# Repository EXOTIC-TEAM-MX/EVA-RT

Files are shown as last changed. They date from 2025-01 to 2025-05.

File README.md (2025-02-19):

# EVA-RT
EVA-RT is the new robotracer series with centrifugal fan and side sensors for curve and goal marks. Created in December 2024 to participate in the All Chile robot Contest 2025, obtaining good results despite its simplicity.

Achievements:
- ACRC2025 - 1st and 2nd place

This repository contains the details, source code, 3D models, PCB files of the robot and EasyEDA proyect available for editing and exporting!

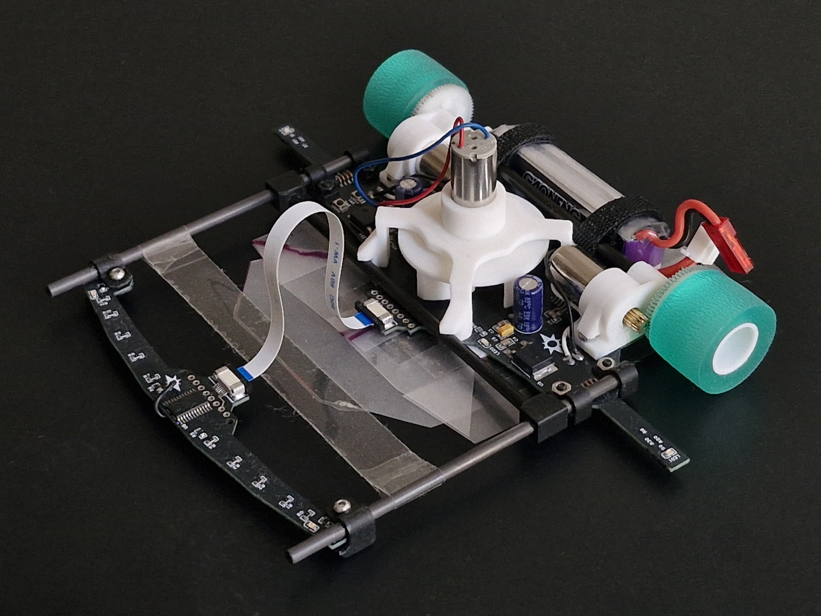
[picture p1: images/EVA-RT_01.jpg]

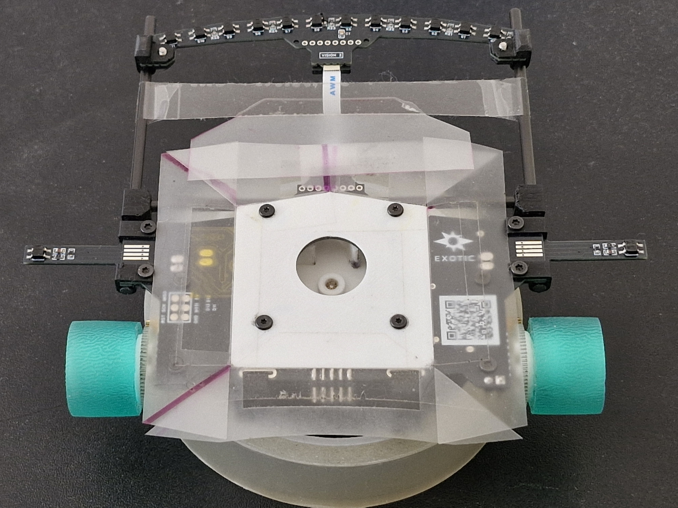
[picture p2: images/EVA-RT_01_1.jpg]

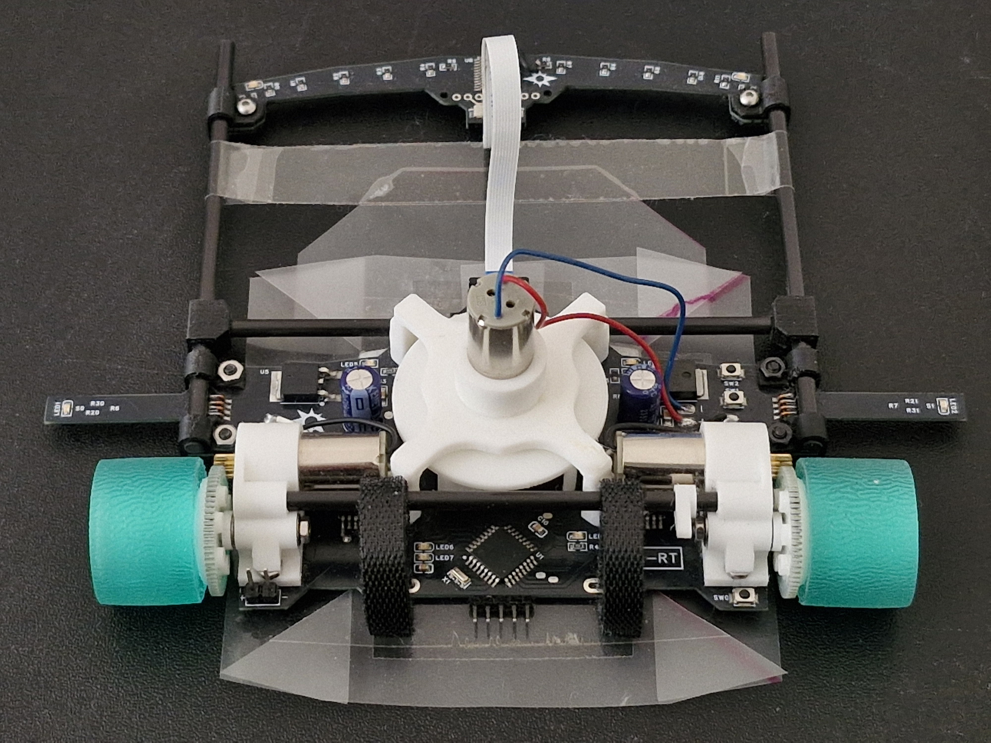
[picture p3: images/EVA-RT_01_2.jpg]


# DETAILS
- Name: EVA-RT
- PCB thickness: 1mm
- Dimensions: 117 x 146 x 38 mm
- Weight: 89g
- MCU: ATMEGA328P-AU
- Line sensor: 12x QRE1113GR
- Side sensor: 2x QRE1113GR
- Motor: 3x coreless 1020 7.4V (unknown model)
- Motor Driver: 2x IFX9201SG, RM10N100LD
- Battery: GAONENG 2S 7.4V 300mAh (80C/160C)
- Gears (M0.3): Spur 64T, pinnion 11T
- Wheel tires: printer rollers (unknown model)

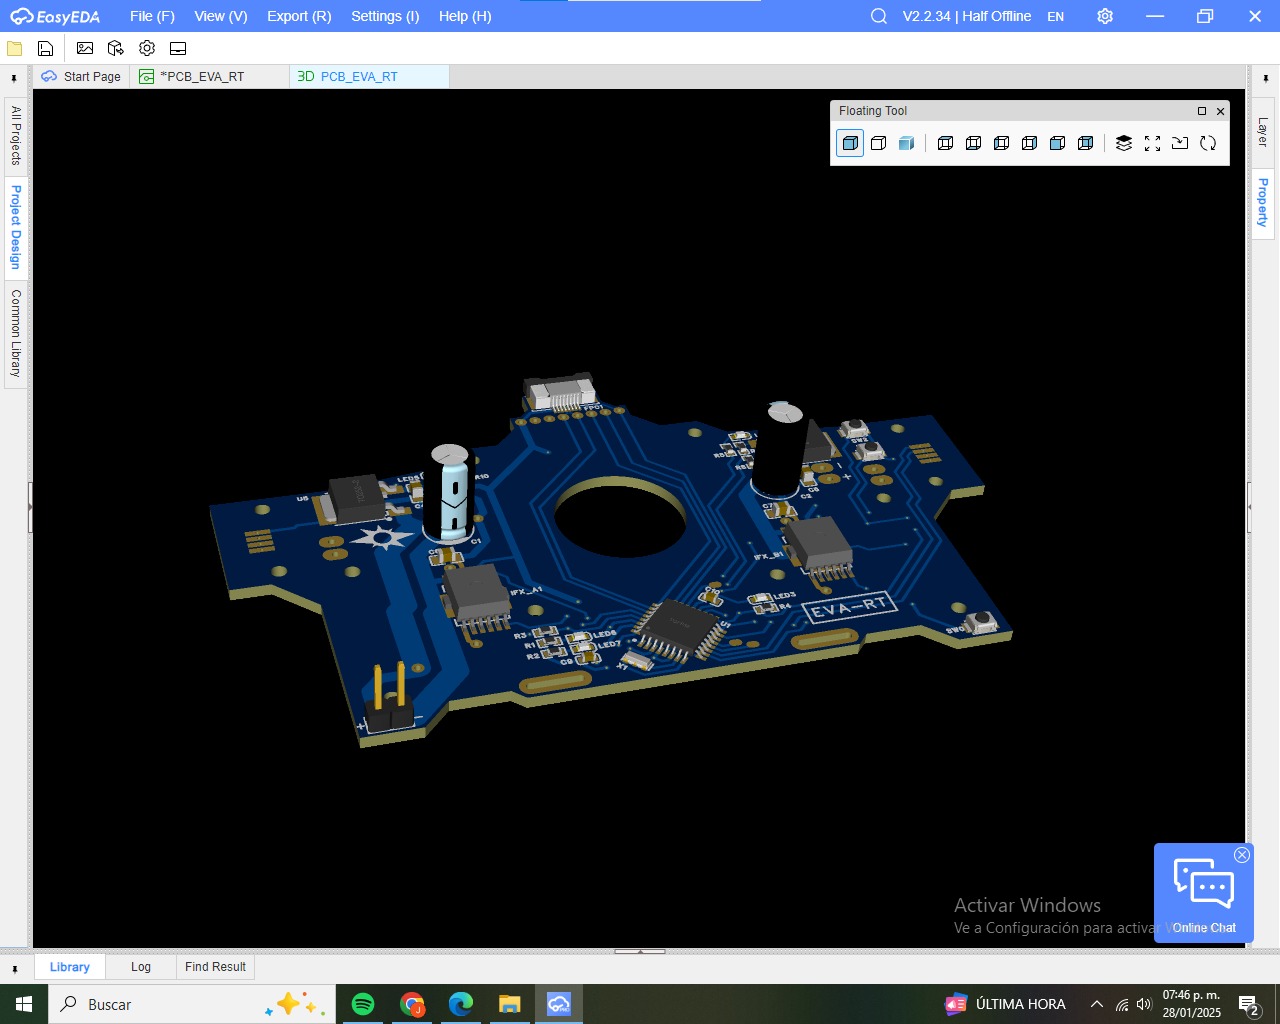
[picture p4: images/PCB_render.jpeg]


# ENVIROMENT
- Arduino IDE 2.0.2
- Autodesk Fusion 360
- EasyEDA-ProV2.2.34.8

#  Robotracer EVA-RT01 code LITE1.0 test
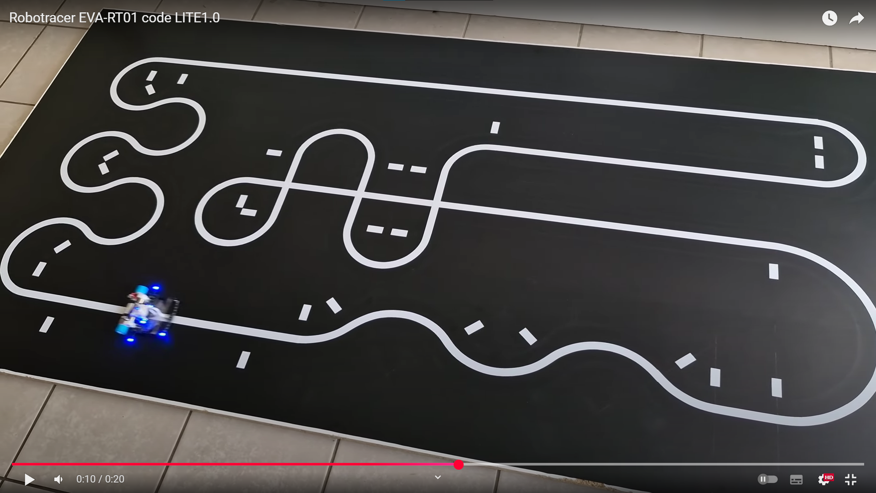
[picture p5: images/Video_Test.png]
(https://youtu.be/mkbgixV5h3M)


# LICENSE
This repository is released under the GNU Affero General Public License v3.0.

©  EXOTIC TEAM MX

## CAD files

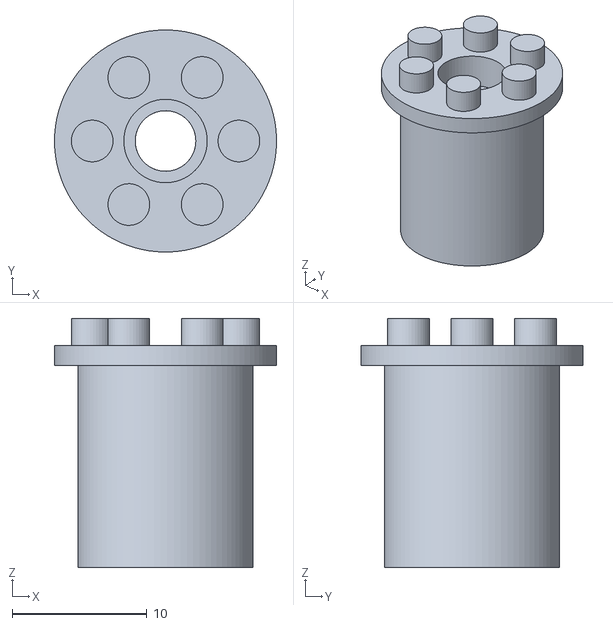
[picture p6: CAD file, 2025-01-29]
3d_models/wheel_rim.stl
16.5 x 16.5 x 18.5

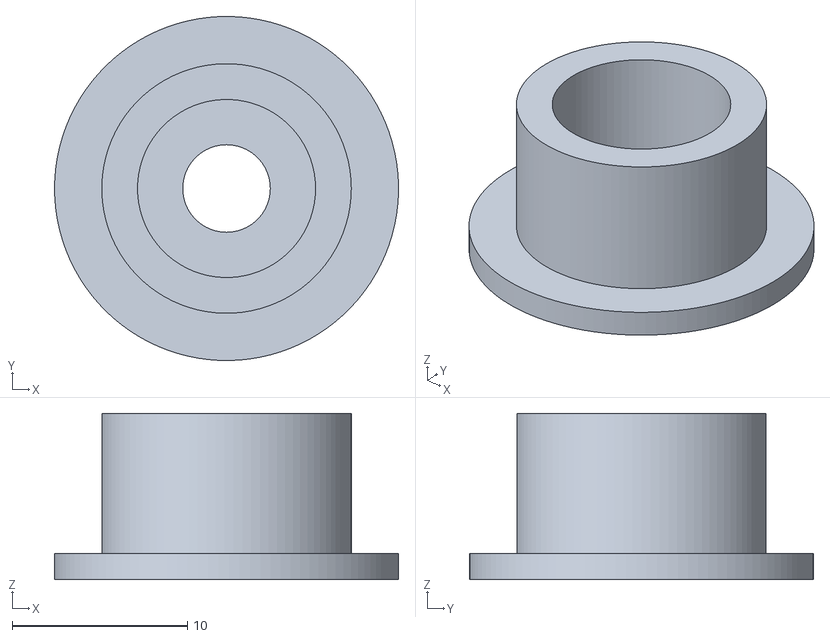
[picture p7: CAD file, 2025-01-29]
3d_models/impeller_base_2.stl
19.6 x 19.6 x 9.50

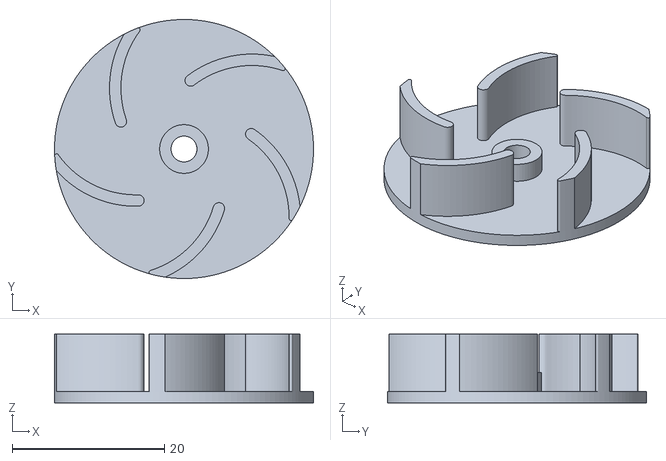
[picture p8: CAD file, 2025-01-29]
3d_models/impeller_fan.stl
34.0 x 34.0 x 9.00

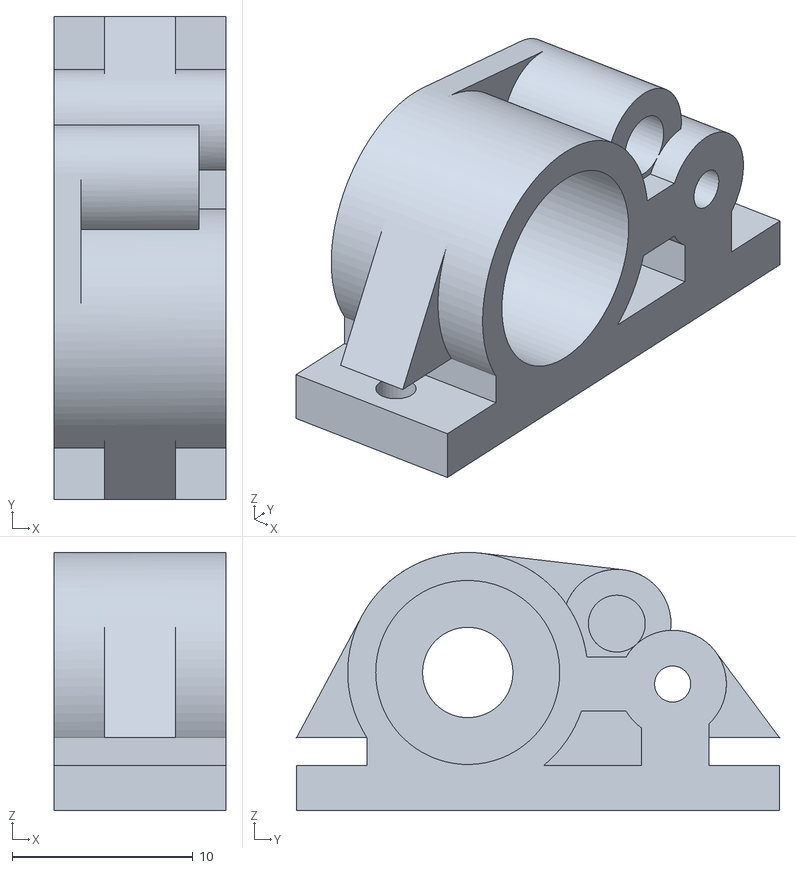
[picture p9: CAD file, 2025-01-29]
3d_models/gearbox.stl
9.50 x 26.7 x 14.3

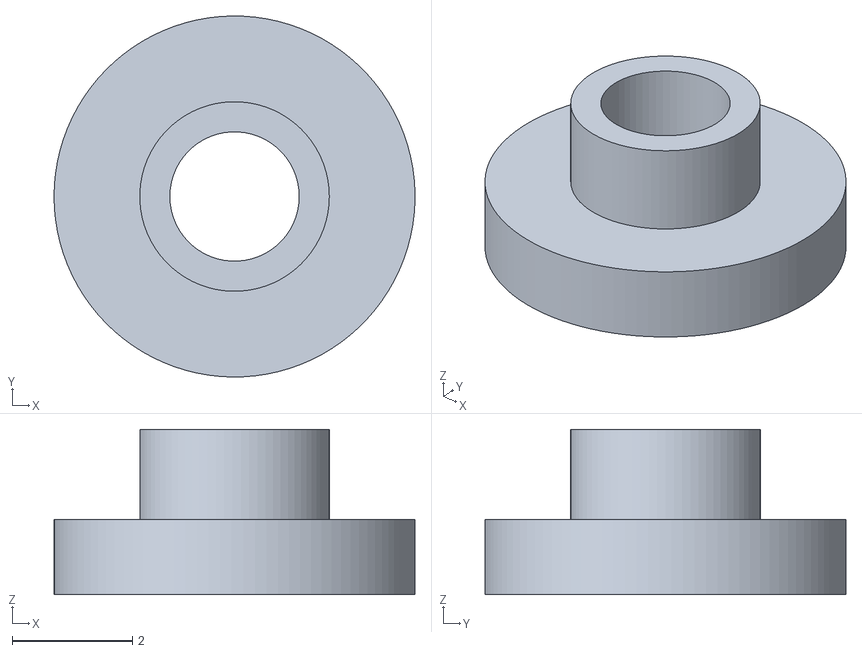
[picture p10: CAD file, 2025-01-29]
3d_models/bead.stl
6.00 x 6.00 x 2.75

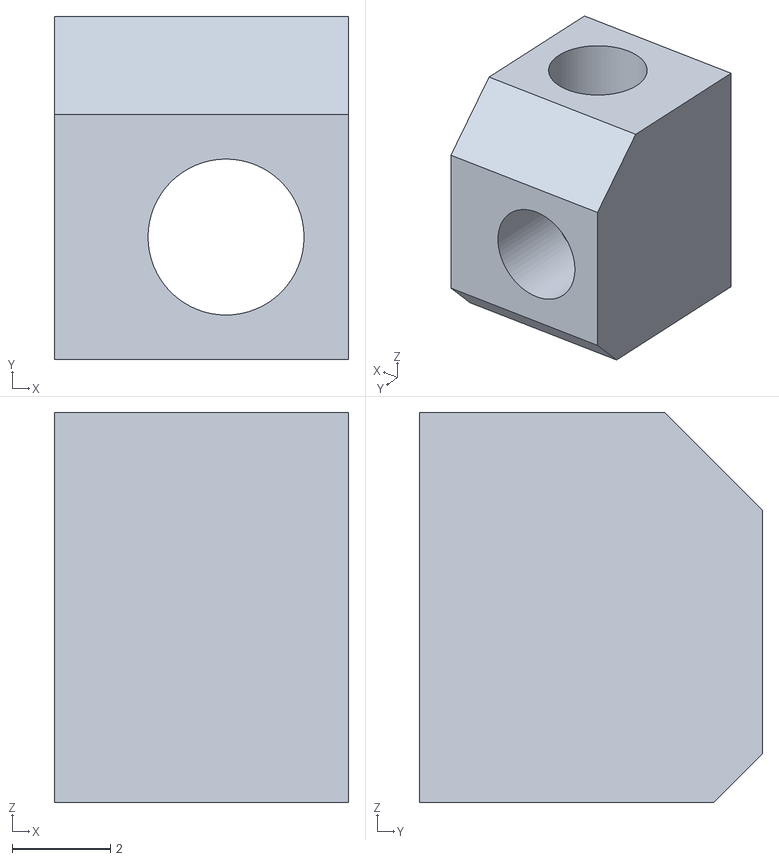
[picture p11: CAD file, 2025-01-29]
3d_models/barilla_connection.stl
6.00 x 7.00 x 7.95

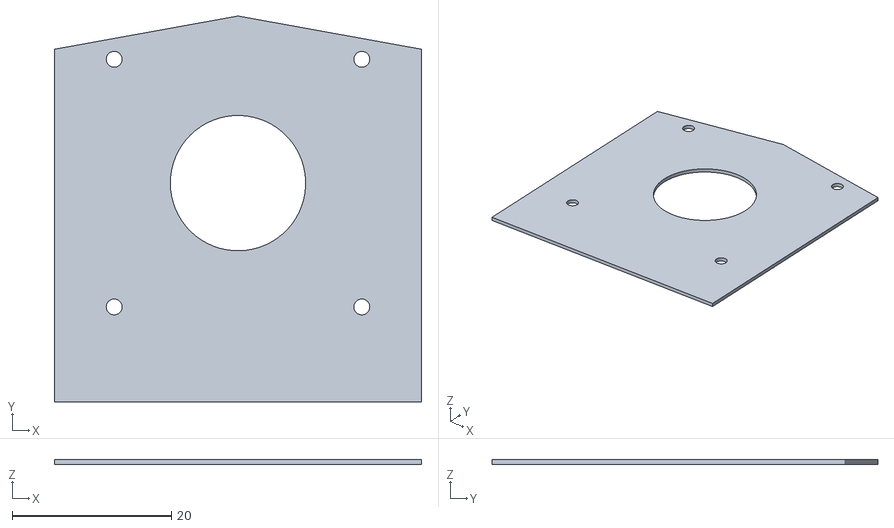
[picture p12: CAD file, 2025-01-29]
3d_models/suction_base.stl
46.2 x 48.5 x 0.6

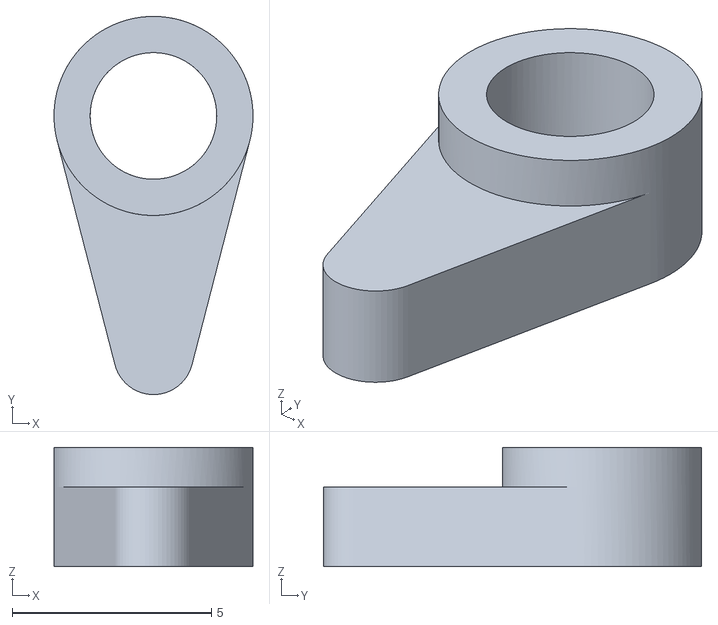
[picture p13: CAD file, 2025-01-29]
3d_models/battery_holder.stl
5.00 x 9.50 x 3.00

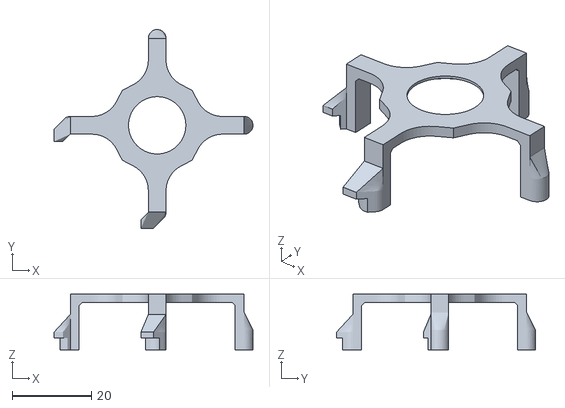
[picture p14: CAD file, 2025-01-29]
3d_models/impeller_base_1.stl
50.4 x 50.4 x 14.1

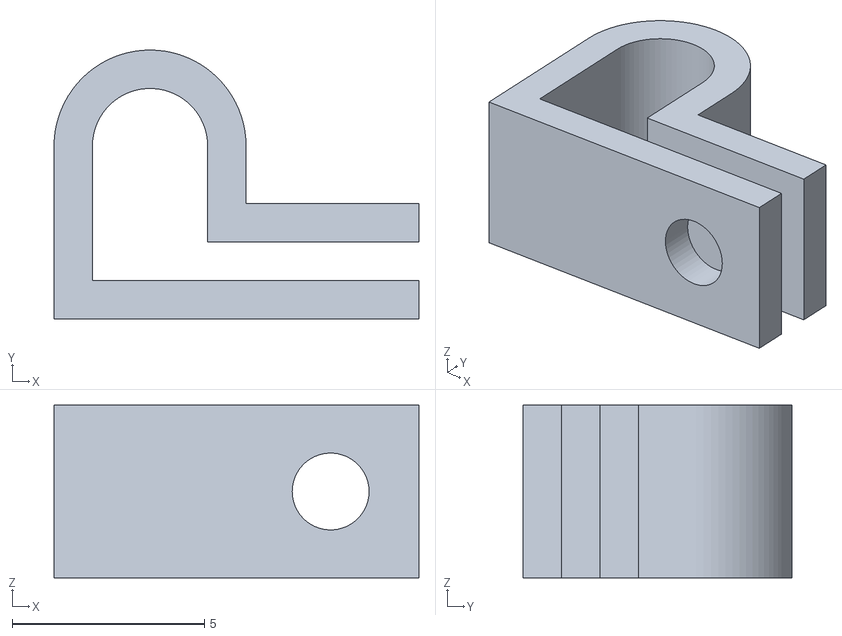
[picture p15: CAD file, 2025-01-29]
3d_models/barilla_clamp.stl
9.50 x 7.00 x 4.50

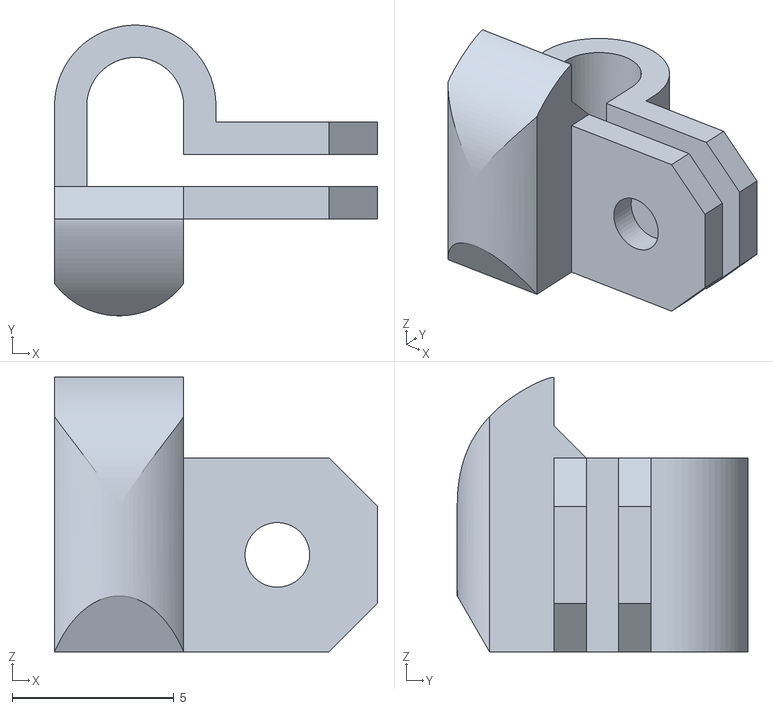
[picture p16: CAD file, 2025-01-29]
3d_models/sensor_sledge.stl
10.0 x 9.00 x 8.50

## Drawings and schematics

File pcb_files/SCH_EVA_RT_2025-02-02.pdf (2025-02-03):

Power Supply & Voltage Regulator | Source Capacitors

## User Interface I/O

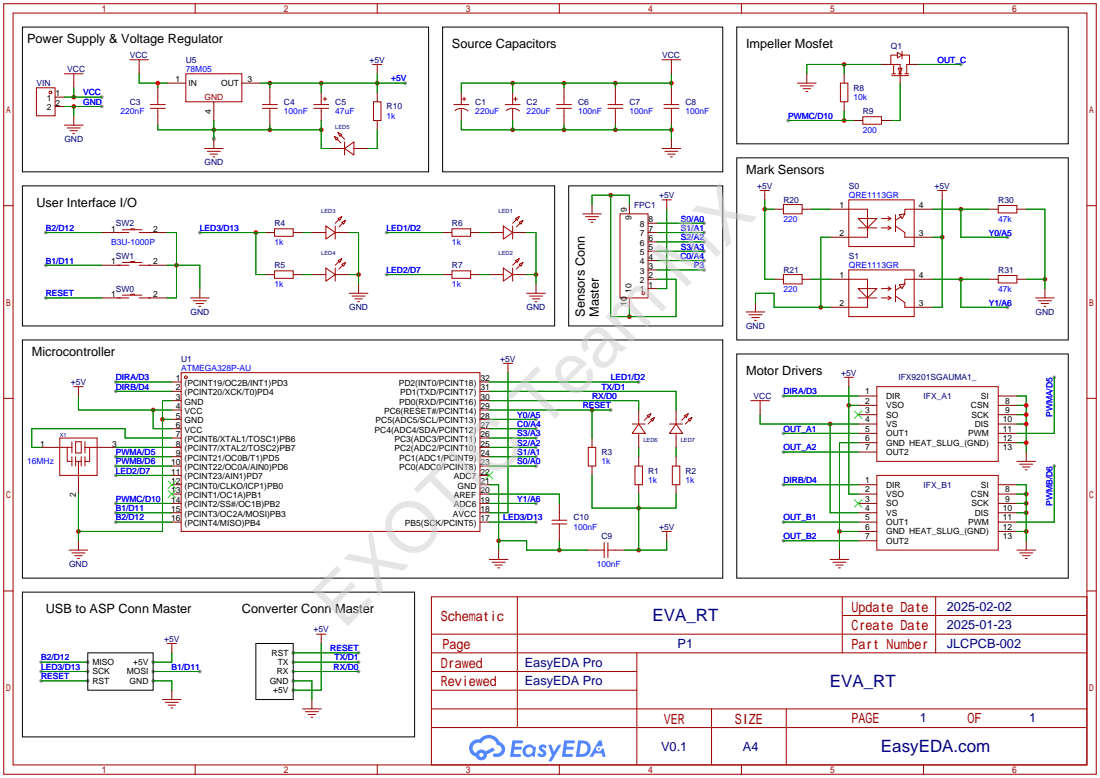
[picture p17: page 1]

USB to ASP Conn Master

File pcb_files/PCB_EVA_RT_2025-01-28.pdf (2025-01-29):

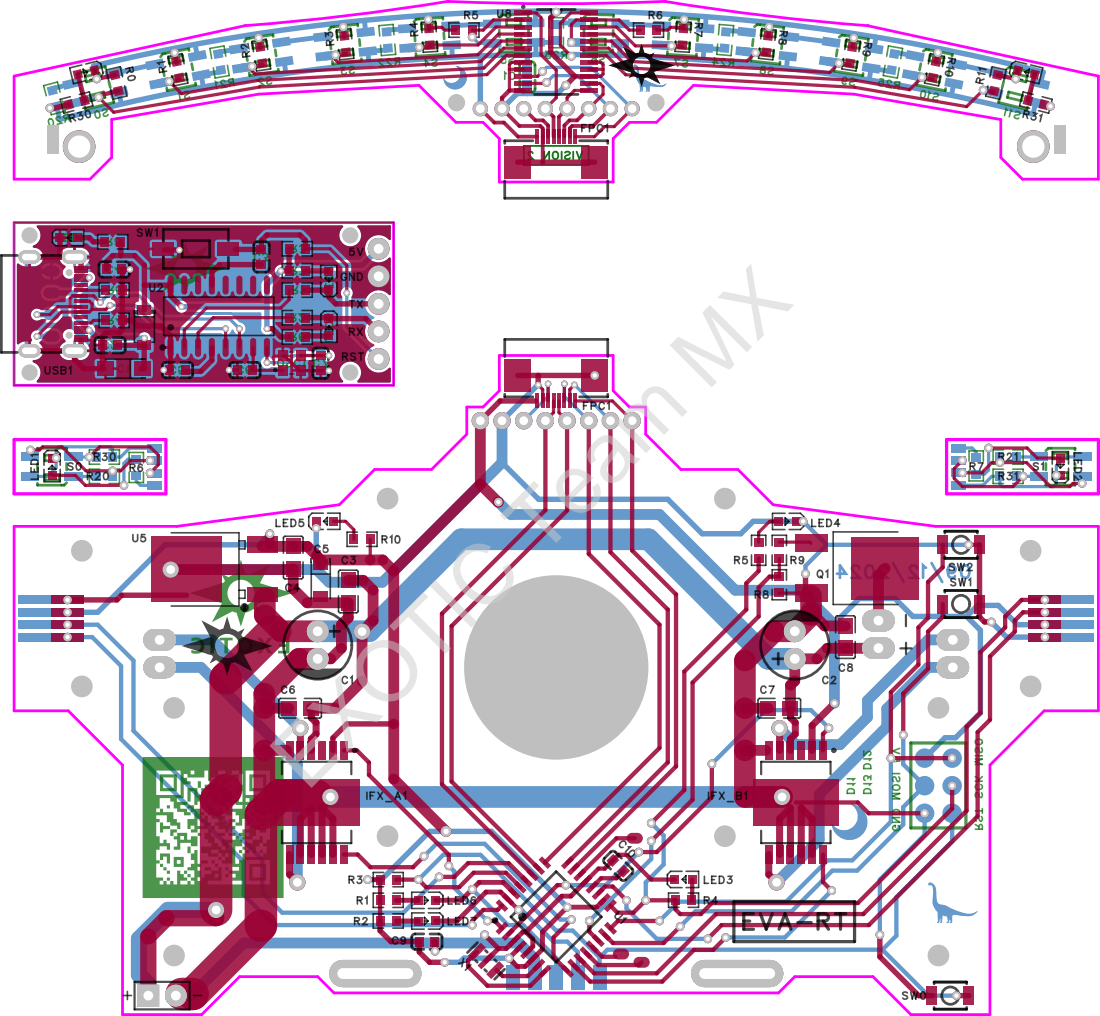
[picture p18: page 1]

U2 | C7LED² LED³ | GND

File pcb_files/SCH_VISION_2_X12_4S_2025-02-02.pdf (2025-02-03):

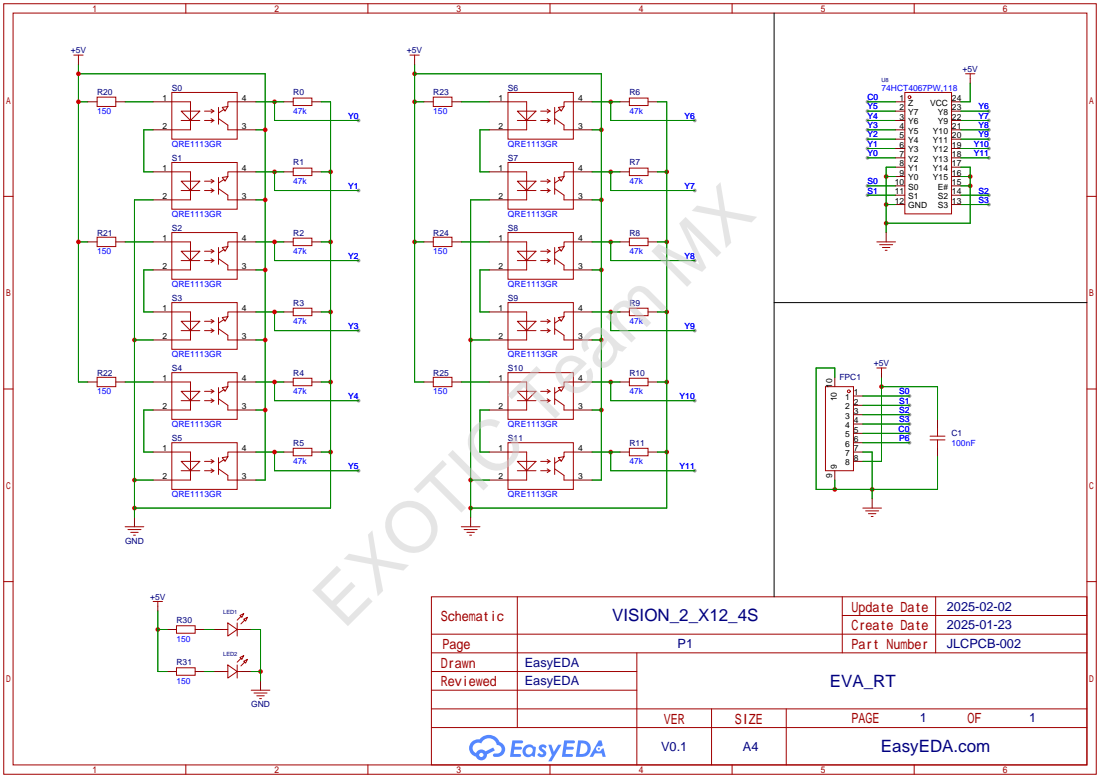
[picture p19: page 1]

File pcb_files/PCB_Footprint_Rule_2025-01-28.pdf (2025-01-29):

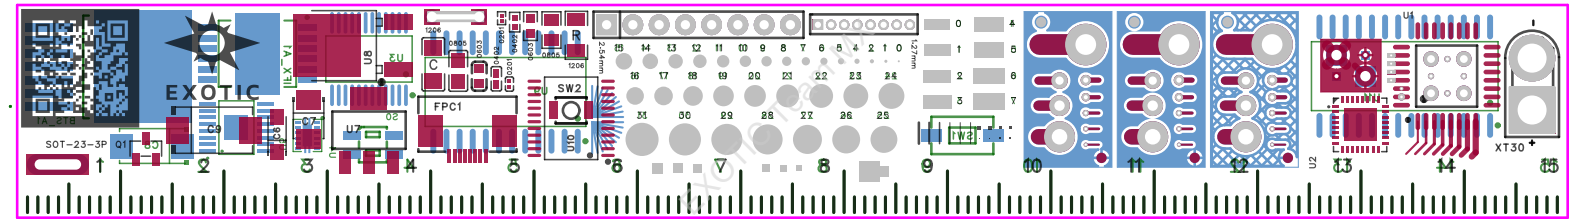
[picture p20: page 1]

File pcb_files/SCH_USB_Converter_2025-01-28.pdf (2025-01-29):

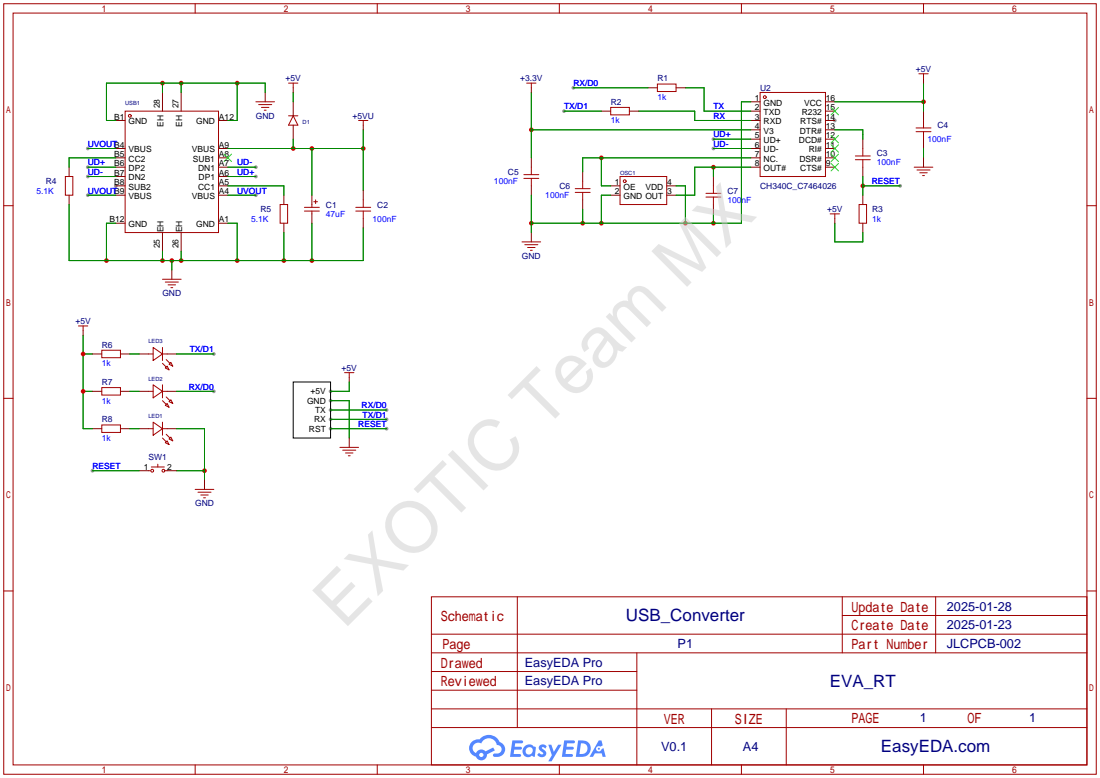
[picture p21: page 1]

DSR# 10 RI# 11 DCD# 12 DTR# 13 RTS# 14 R232 15 VCC 16

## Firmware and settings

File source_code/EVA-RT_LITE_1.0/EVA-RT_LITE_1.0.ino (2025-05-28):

/*
  EVA-RT LITE v1.0 - main code for robotracer EVA-RT series
  
    Created on: Jan, 2025
    Edited by Mauricio Tovar
  
      DRIVERS:            IXF9201SG
      NUMBER OF SENSORS:  12A/3s
      MICROCONTROLLER:    ATMEGA328P-AU
      BATTERY:            2S
      CONTROL:            PD
      MOTORS:             1020

  This code is the simplified version of the program used for
  the All Chile Robot Contest 2025. Conceived and designed to
  facilitate the reading and understanding of the fundamental
  concepts.

  This code consists of the base control of the robot using the
  functions included in the Arduino core library. It includes
  the reading of the side sensors for detecting the goal marker.

  Copyright (C) 2025 EXOTIC TEAM MX

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
  This code is part of the EVA-RT Github repository. See more
  in the next link:
  
  https://github.com/EXOTIC-TEAM-MX/EVA-RT
*/

//  =============================
//  U S E R   P A R A M E T E R S
//  =============================

#define KP 0.04  //  proportional component coefficient (0.04)
#define KD 0.6   //  derivative component coefficient (0.6)

#define SPEED 60       //  base PWM motors speed value (60)(min 20)
#define SPEED_IMP 215  //  base PWM impeller speed value (215)

#define INVERT_SENSOR_READS false  //  white line and black background if false (true = black line)

#define SPEED_TIME_MS 50    //  time until robot gets base speed (50)
#define RUN_TIME_MS 6000    //  time until robot turns off automatically since start running (6000)
#define MAX_OUT_TIME_MS 10  //  maximum time sensors can be out of line until robot turns off (10)

//  =====================================
//  A D V A N C E D   P A R A M E T E R S
//  =====================================

#define OUT_OUTTER_SPEED 255  //  outter side motor PWM value when sensors are offline (255)
#define OUT_INNER_SPEED -255  //  inner side motor PWM value when sensors are offline (-255)
#define MAX_IMP_SPEED 200     //  max impeller PWM value (200)

#define MARK_TIMER_MS 50     //  time while mark state is enabled (50)
#define START_DELAY_MS 1000  //  time before robot start running (1000)
#define STOP_TIME_MS 75      //  time while robot is breaking after is turned off (75)

#define SENSOR_THRESHOLD_PERCENT 75
#define CALIBRATION_NOISE_DIVISOR 8
#define CALIBRATION_AVG_SAMPLES 8
#define CALIBRATION_COLLECTOR_SAMPLES 10

//  ===============================
//  G L O B A L   C O N S T A N T S
//  ===============================

//  user input pins
#define PIN_BUTTON_1 11
#define PIN_BUTTON_2 12
#define PIN_LED_1 2
#define PIN_LED_2 7
#define PIN_LED_3 13

//  sensor pins
#define PIN_SENSORS_MUX_S0 A0
#define PIN_SENSORS_MUX_S1 A1
#define PIN_SENSORS_MUX_S2 A2
#define PIN_SENSORS_MUX_S3 A3
#define PIN_SENSORS_COMMON A4
#define PIN_MARK_SENSOR_0 A5
#define PIN_MARK_SENSOR_1 A6

//  motor driver pins
#define PIN_PWM_A 5
#define PIN_PWM_B 6
#define PIN_PWM_C 10
#define PIN_DIR_A 3
#define PIN_DIR_B 4

#define NUM_SENSORS 12      //  ammount of line sensors
#define NUM_MARK_SENSORS 2  //  ammount of side mark sensors
#define TOTAL_SENSORS (NUM_SENSORS + NUM_MARK_SENSORS)
#define INDEX_MS0 NUM_SENSORS
#define INDEX_MS1 (NUM_SENSORS + 1)
#define FIRST_SENSOR_MUX_SWITCH_CONFIG 2  //  mux switch configuration for first line sensor (S0)
#define LAST_SENSOR_MUX_SWITCH_CONFIG 13  //  mux switch configuration for last line sensor (S11)

//  ===============================
//  G L O B A L   V A R I A B L E S
//  ===============================

int sensorValues[TOTAL_SENSORS];
unsigned int maxSensorValues[TOTAL_SENSORS];
unsigned int minSensorValues[TOTAL_SENSORS];
int sensorThreshold[TOTAL_SENSORS];

bool markState[2];
bool pastMarkSensorValues[2];

unsigned long startTime;              //  instant time before start running
unsigned long currentTime;            //  current time
unsigned long outStartTime;           //  last time before sensors gets offline
unsigned long markRisingEdgeTime[2];  //  instant time when marks sensors reads rising edge

bool isOnLine = false;
bool lastDetectedSide;
bool isRunning = false;
bool isOffEnabled = false;

int speedDecrement = 0;
bool isSpeedBase = false;

int error;
int previousError;

void setup() {
  //  ===================
  //  M A I N   S E T U P
  //  ===================

  //  user I/O interface setup
  pinMode(PIN_BUTTON_1, INPUT_PULLUP);
  pinMode(PIN_BUTTON_2, INPUT_PULLUP);
  pinMode(PIN_LED_1, OUTPUT);
  pinMode(PIN_LED_2, OUTPUT);
  pinMode(PIN_LED_3, OUTPUT);

  //  sensor switch pins setup
  pinMode(PIN_SENSORS_MUX_S0, OUTPUT);
  pinMode(PIN_SENSORS_MUX_S1, OUTPUT);
  pinMode(PIN_SENSORS_MUX_S2, OUTPUT);
  pinMode(PIN_SENSORS_MUX_S3, OUTPUT);

  //  motor driver pins setup
  pinMode(PIN_DIR_A, OUTPUT);
  pinMode(PIN_DIR_B, OUTPUT);

  //  =========================
  //  R O B O T   B O O T I N G
  //  =========================

  //  boot display animation
  digitalWrite(PIN_LED_3, HIGH);
  delay(750);
  digitalWrite(PIN_LED_3, LOW);

  //  calibration button trigger
  while (digitalRead(PIN_BUTTON_1)) {
  };

  //  ===================================
  //  S E N S O R   C A L I B R A T I O N
  //  ===================================
  delay(250);
  resetCalibrationValues();

  while (digitalRead(PIN_BUTTON_1)) {
    PINB |= 1 << 5;  //  toggle LED 3
    calibrateSensors();
  }
  digitalWrite(PIN_LED_3, LOW);
  delay(250);

  //  get sensor threshold
  for (byte i = 0; i < TOTAL_SENSORS; i++) {
    sensorThreshold[i] = (maxSensorValues[i] - minSensorValues[i]) * ((float)(SENSOR_THRESHOLD_PERCENT) / 100) + minSensorValues[i];
  }

  //  =======================
  //  R E A D Y   T O   R U N
  //  =======================

  //  start run button trigger
  while (digitalRead(PIN_BUTTON_1)) {
  };
  digitalWrite(PIN_LED_3, HIGH);
  delay(250);
  digitalWrite(PIN_LED_3, LOW);

  delay(1000);  //  wait 1 second to enable the impeller

  digitalWrite(PIN_LED_1, HIGH);
  digitalWrite(PIN_LED_2, HIGH);
  setImpeller(SPEED_IMP);
  delay(START_DELAY_MS);
  //  must stop impeller until motors speed gets half of base speed value
  setImpeller(0);
  digitalWrite(PIN_LED_3, HIGH);

  //  set start values
  isRunning = true;

  startTime = millis();
  currentTime = startTime;
  outStartTime = startTime;
}

//  =============================================================
//                    R U N N I N G    L O O P
//  =============================================================

void loop() {
  while (isRunning) {
    //  get current time
    currentTime = millis();

    //  speed increase method
    if (!isSpeedBase) {
      //  if running elapsed time is higher or equal to SPEED_TIME_MS
      //  set impeller speed and set speed decrement value to zero
      if (currentTime - startTime >= SPEED_TIME_MS) {
        setImpeller(SPEED_IMP);
        speedDecrement = 0;
        isSpeedBase = true;
      } else {
        //  interpolate speed decrement ramp value in function of time elapsed after start running
        speedDecrement = SPEED - (SPEED * (currentTime - startTime) / SPEED_TIME_MS);

        //  set impeller speed at mid of speed decrement ramp time
        if (currentTime - startTime >= SPEED_TIME_MS / 2) {
          setImpeller(SPEED_IMP);
        }
      }
    }

    //  get position and error
    unsigned int position = readLine();
    error = position - (NUM_SENSORS - 1) * 1000 / 2;

    //  calculate error difference
    int deltaError = error - previousError;
    previousError = error;  //  update previous error after

    updateMarkState();

    //  if is online and position is no equal to the limits, calculate control signal and PWM values
    if (isOnLine && position && position != (NUM_SENSORS - 1) * 1000) {
      //  check the last detected side of the line
      if (sensorValues[0] || sensorValues[1]) {
        lastDetectedSide = 0;
      }
      if (sensorValues[NUM_SENSORS - 1] || sensorValues[NUM_SENSORS - 2]) {
        lastDetectedSide = 1;
      }

      //  calculate control signal
      long controlSignal = (error * KP) + ((long)(deltaError)*KD);

      //  constrain control signal
      controlSignal = constrain(controlSignal, -510, 510);

      //  get motor PWM values
      int valPWMA = SPEED + controlSignal - speedDecrement;
      int valPWMB = SPEED - controlSignal - speedDecrement;

      //  constrain motor PWM values
      valPWMA = constrain(valPWMA, -255, 255);
      valPWMB = constrain(valPWMB, -255, 255);

      //  set motors PWM
      setMotors(valPWMA, valPWMB);

      outStartTime = currentTime;  //  update last time online
    } else {
      //  ===================================
      //  O U T   O F   L I N E   M E T H O D
      //  ===================================

      //  get out elapsed time
      unsigned long outElapsedTime = currentTime - outStartTime;

      //  if out elapsed time is higher or equal to MAX_OUT_TIME_MS, stop running
      if (outElapsedTime >= MAX_OUT_TIME_MS) { isRunning = false; }

      //  set motors in function of last detected side before out
      if (!lastDetectedSide) {
        setMotors(OUT_INNER_SPEED, OUT_OUTTER_SPEED);  //  robot turns left
      } else {
        setMotors(OUT_OUTTER_SPEED, OUT_INNER_SPEED);  //  robot turns right
      }
    }

    //  button off trigger
    isRunning = (!digitalRead(PIN_BUTTON_1) || !digitalRead(PIN_BUTTON_2)) ? false : isRunning;

    //  off by running time trigger
    if (currentTime - startTime >= RUN_TIME_MS) { isRunning = false; }

    //  update previous mark sensor values
    pastMarkSensorValues[0] = sensorValues[INDEX_MS0];
    pastMarkSensorValues[1] = sensorValues[INDEX_MS1];
  }

  //  =============================================================
  //                    R U N N I N G    S T O P
  //  =============================================================

  setMotors(-SPEED, -SPEED);  //  instant brake
  digitalWrite(PIN_LED_3, LOW);
  delay(75);  //  brake time

  setMotors(0, 0);
  digitalWrite(PIN_LED_1, LOW);
  digitalWrite(PIN_LED_2, LOW);
  digitalWrite(PIN_LED_3, HIGH);

  delay(250);
  setImpeller(0);
  delay(2000);  //  two seconds delay after robot gets goal (very important)
  digitalWrite(PIN_LED_3, LOW);

  //  robot end programm animation
  while (1) {
    digitalWrite(PIN_LED_1, HIGH);
    digitalWrite(PIN_LED_2, HIGH);
    delay(50);
    digitalWrite(PIN_LED_1, LOW);
    digitalWrite(PIN_LED_2, LOW);
    delay(1000);
  }
}

void updateMarkState() {
  for (byte i = 0; i < 2; i++) {
    //  save instant time on rising edge
    if (sensorValues[INDEX_MS0 + i] && !pastMarkSensorValues[i]) {
      markRisingEdgeTime[i] = currentTime;
      markState[i] = true;

      //  if right mark is detected, set off enable flag to true
      //  if left mark is detected, set to false
      isOffEnabled = i ? true : false;
    }

    if (markState[i]) {
      //  set off enable flag while left mark state is true
      if (!i) { isOffEnabled = false; }

      //  set mark state to false if its elapsed time is higher or equal to MARK_TIMER_MS
      if (currentTime - markRisingEdgeTime[i] >= MARK_TIMER_MS) {
        markState[i] = false;
        //  if index is higher to zero (right mark index), off enabled flag is true
        //  and if 1 second has passed since robot started running
        if (i && isOffEnabled && currentTime - startTime >= 1000) {
          isRunning = false;  // comment this line to disable goal mark stop
        }
      }
    }
  }
}

//  resets minimum and maximum sensor values
void resetCalibrationValues() {
  for (byte i = 0; i < TOTAL_SENSORS; i++) {
    maxSensorValues[i] = 0;
    minSensorValues[i] = 1023;
  }
}

//  returns line position using weighted average calculation
unsigned int readLine() {
  uint32_t wtd = 0;  //  temporal sum of weighted sensor values
  uint32_t sum = 0;  //  temporal sum of sensor values
  isOnLine = false;  //  set line is not on sensors range at the start of line position calculation

  //  get calibrated sensor read values
  readCalibratedSensors();

  for (byte i = 0; i < NUM_SENSORS; i++) {
    //  add to sum if actual sensor value is higher to zero
    if (sensorValues[i]) {
      isOnLine = true;  // updates to true if at least one sensor detects the line
      wtd += (uint32_t)sensorValues[i] * i * 1000;
      sum += sensorValues[i];
    }
  }

  //  if weighted sum is higher to zero return weighted average
  return wtd ? wtd / sum : 0;
}

//  updates sensor values with direct raw measurements (inverted or not inverted)
void readRawSensors() {
  //  line sensor reading loop
  for (byte i = FIRST_SENSOR_MUX_SWITCH_CONFIG; i <= LAST_SENSOR_MUX_SWITCH_CONFIG; i++) {
    PORTC = (PORTC & ~0b1111) | i;                                                      //  set mux switch address direct from I/O registers
    sensorValues[i - FIRST_SENSOR_MUX_SWITCH_CONFIG] = analogRead(PIN_SENSORS_COMMON);  //  read analog value from mux common pin
  }

  //  read analog value from mark sensor pins
  sensorValues[INDEX_MS0] = analogRead(PIN_MARK_SENSOR_0);
  sensorValues[INDEX_MS1] = analogRead(PIN_MARK_SENSOR_1);

  //  sensor values invert method
  if (INVERT_SENSOR_READS) {
    for (byte i = 0; i < TOTAL_SENSORS; i++) {
      sensorValues[i] = 1023 - sensorValues[i];
    }
  }
}

//  updates sensor values with sampled average raw measurements
void readSampledSensors() {
  int sumSensorValues[TOTAL_SENSORS];  //  temporal sum of each sensor samples

  //  set sum values to zero
  for (byte i = 0; i < TOTAL_SENSORS; i++) {
    sumSensorValues[i] = 0;
  }

  for (byte j = 0; j < CALIBRATION_AVG_SAMPLES; j++) {
    //  update raw sensor values
    readRawSensors();

    //  adds readings to sum of each sensor
    for (byte i = 0; i < TOTAL_SENSORS; i++) {
      sumSensorValues[i] += sensorValues[i];
    }
  }

  //  update sensor values with sum average
  for (byte i = 0; i < TOTAL_SENSORS; i++) {
    sensorValues[i] = (sumSensorValues[i] + (CALIBRATION_AVG_SAMPLES >> 1)) / CALIBRATION_AVG_SAMPLES;
  }
}

//  calculates fixed range raw sensor values
void readCalibratedSensors() {
  //  get actual raw sensor readings
  readRawSensors();

  for (byte i = 0; i < NUM_SENSORS; i++) {
    unsigned int range = maxSensorValues[i] - sensorThreshold[i];

    if (sensorValues[i] > sensorThreshold[i]) {
      if (sensorValues[i] < maxSensorValues[i]) {
        //  scale value to fixed range if raw sensor value is higher than threshold and lower than maximum
        sensorValues[i] = ((sensorValues[i] - sensorThreshold[i]) * 255) / range;
      } else {
        sensorValues[i] = 255;  //  set to 255 if raw sensor value is higher than maximum calibrated value
      }
    } else {
      sensorValues[i] = 0;  //  set to zero if raw sensor value is lower than threshold
    }
  }

  //  set mark sensors values to 1 if its raw value is higher than threshold
  sensorValues[INDEX_MS0] = sensorValues[INDEX_MS0] > sensorThreshold[INDEX_MS0];
  sensorValues[INDEX_MS1] = sensorValues[INDEX_MS1] > sensorThreshold[INDEX_MS1];
}

//  updates minimum and maximum sensor values
void calibrateSensors() {
  int highestSample[TOTAL_SENSORS];  //  temporal highest collector sample for each sensor
  int lowestSample[TOTAL_SENSORS];   //  temporal lowest collector sample for each sensor

  //  samples recollector
  for (byte j = 0; j < CALIBRATION_COLLECTOR_SAMPLES; j++) {
    readSampledSensors();

    for (byte i = 0; i < TOTAL_SENSORS; i++) {
      //  update maximum value collected
      if ((j == 0) || (sensorValues[i] > highestSample[i])) {
        highestSample[i] = sensorValues[i];
      }

      //  update minimum value collected
      if ((j == 0) || (sensorValues[i] < lowestSample[i])) {
        lowestSample[i] = sensorValues[i];
      }
    }
  }

  //  update the min and max values
  for (byte i = 0; i < TOTAL_SENSORS; i++) {
    // update maximum only if the min of all collected readings was still higher than it
    // (we got all collected readings in a row higher than the existing maximum)
    if (lowestSample[i] > maxSensorValues[i]) {
      maxSensorValues[i] = lowestSample[i];
    }

    // update minimum only if the max of all collected readings was still lower than it
    // (we got all collected readings in a row lower than the existing minimum)
    if (highestSample[i] < minSensorValues[i]) {
      minSensorValues[i] = highestSample[i];
    }
  }
}

//  updates impeller PWM duty values
void setImpeller(int _pwm) {
  analogWrite(PIN_PWM_C, constrain(_pwm, 0, 255));
}

//  updates both motors PWM duty values
void setMotors(int _pwm_a, int _pwm_b) {
  //  set direction output on motor A
  if (_pwm_a > 0) {
    digitalWrite(PIN_DIR_A, LOW);  //  forward
  } else if (_pwm_a < 0) {
    digitalWrite(PIN_DIR_A, HIGH);  //  reverse
  }

  //  set direction output on motor B
  if (_pwm_b > 0) {
    digitalWrite(PIN_DIR_B, LOW);  //  forward
  } else if (_pwm_b < 0) {
    digitalWrite(PIN_DIR_B, HIGH);  //  reverse
  }

  //  update PWM duty on motor drivers
  analogWrite(PIN_PWM_A, abs(_pwm_a));
  analogWrite(PIN_PWM_B, abs(_pwm_b));
}

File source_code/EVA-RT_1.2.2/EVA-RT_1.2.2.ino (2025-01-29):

/*
  EVA-RT v1.2.2 - main code for robotracer EVA-RT series

    Created on: Jan, 2025
    Edited by Mauricio Tovar

      DRIVERS:            IXF9201SG
      NUMBER OF SENSORS:  12A/3s
      MICROCONTROLLER:    ATMEGA328P-AU
      BATTERY:            2S
      CONTROL:            PD
      MOTORS:             1020

  This code is the original version used in the All Chile
  Robot Contest 2025.

  This code consist of the main code for line control,
  interacting directly with the microcontroller registers
  in order to optimize execution time and memory space.

  The code was made in order to develop, test and debug all
  the functions and algorithms of the robot, which is why it
  includes a series of diagnostic tools that facilitate the
  visualization of all these methods. So there may be errors
  and/or bad programming practices.

    Copyright (C) 2025 EXOTIC TEAM MX

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
  This code is part of the EVA-RT Github repository. See more
  in the next link:
  
  https://github.com/EXOTIC-TEAM-MX/EVA-RT
*/

//  ===================================
//  C O N S T A N T   V A R I A B L E S
//  ===================================

#define DM_NO_MODE 0            //  no display mode enabled
#define DM_RUN 1                //  turn LED C while robot is running
#define DM_SPEED_INCREMENT 2    //  start speed increment method
#define DM_OUT_DIRECTION 3      //  turn LED on last side detected
#define DM_COUNTERCORRECTION 4  //  counter correction times
#define DM_MARK_SENSORS 5       //  turns LED while mark is detected
#define DM_MARK_TIMERS 6        //  turns LED while mark state is enabled
#define DM_MARK_EDGES 7         //  turns LED on rising edges and turns down on down edges
#define DM_CROSS_METHODS 8      //  cross methods

//  user input pins
#define PIN_BUTTON_1 11
#define PIN_BUTTON_2 12
#define PIN_LED_1 2
#define PIN_LED_2 7
#define PIN_LED_3 13

//  sensor pins
#define PIN_SENSORS_COMMON A0
#define PIN_SENSORS_SWITCH_0 A1
#define PIN_SENSORS_SWITCH_1 A1
#define PIN_SENSORS_SWITCH_2 A2
#define PIN_SENSORS_SWITCH_3 A3
#define PIN_MARK_SENSOR_0 A5
#define PIN_MARK_SENSOR_1 A6

//  motor driver pins
#define PIN_PWM_A 5
#define PIN_PWM_B 6
#define PIN_PWM_C 10
#define PIN_DIR_A 3
#define PIN_DIR_B 4

#define ADC_GND_CHANNEL 0b1111
#define ADC_MUX_CHANNEL 0b0100
#define ADC_MARK_SENSOR_0 0b0101  //0b0101
#define ADC_MARK_SENSOR_1 0b0110  //0b0110
#define ADC_START_CONVERSION 0b11000000
#define SENSOR_SWITCH_MASK 0b1111

#define NUM_SENSORS 12
#define NUM_MARK_SENSORS 2
#define TOTAL_SENSORS NUM_SENSORS + NUM_MARK_SENSORS
#define INDEX_MS0 NUM_SENSORS
#define INDEX_MS1 NUM_SENSORS + 1
#define FIRST_SENSOR_SWITCH_CONFIG 2
#define LAST_SENSOR_SWITCH_CONFIG 13

#define OUT_OUTTER_SPEED 255
#define OUT_INNER_SPEED -255

#define MAX_IMP_SPEED 245
#define MIN_MARK_TIMER_MS 10
#define MIN_CROSS_WARNING_TIME_MS 20

//  SPEED 40 VALUES: MRK_T_MS(30) CW_T_MS(60) IMP(180)
//  SPEED 60 VALUES: MRK_T_MS(20) CW_T_MS(40) IMP(235)

//  =================================
//  C O N T R O L   V A R I A B L E S
//  =================================

#define ALPHA 1
#define KP 0.06
#define KD 0.6

#define SPEED 40
#define SPEED_IMP 180

#define RUN_TIME_MS 10000
#define SPEED_TIME_MS 10
#define MAX_OUT_TIME_MS 10
#define RUN_TIME_INCREMENT_S 1000

#define STOP_TIME_MS 75

//  ===================================
//  A D V A N C E D   V A R I A B L E S
//  ===================================

#define START_WAIT_MS 1000
#define START_DELAY_MS 1000
#define INVERT_SENSOR_READS false
byte DISPLAY_MODE = DM_RUN;

bool isConsoleMode = false;
bool areMotorsEnabled = true;

#define MARK_TIMER_MS 30
#define SENSOR_MASK false

#define SENSOR_THRESHOLD_PERCENT 75
#define CALIBRATION_NOISE_DIVISOR 8
#define CALIBRATION_AVG_SAMPLES 8
#define CALIBRATION_COLLECTOR_SAMPLES 10

#define CROSS_SENSOR_OFSET 3
#define CORRECT_CROSS_ERROR true
#define CROSS_WARNING_METHOD false
#define CROSS_WARNING_TIME_MS 60

#define FIXED_MAX_TIME_VALUES false
#define FIXED_MIN_TIME_VALUES false

//  =================================
//  P R I V A T E   V A R I A B L E S
//  =================================

int sensorValues[TOTAL_SENSORS];
unsigned int maxSensorValues[TOTAL_SENSORS];
unsigned int minSensorValues[TOTAL_SENSORS];
byte sensorThreshold[TOTAL_SENSORS];
bool previousLinePrint[NUM_SENSORS];

bool markState[2];
bool pastMarkSensorValues[2];

unsigned long startTime;
unsigned long currentTime;
unsigned long outStartTime;
unsigned long correctionStartTime;
unsigned long runTime = RUN_TIME_MS;
unsigned long markDetectedTime[2];
unsigned long crossStartTime;

bool isOnLine = false;
bool lastDetectedSide;
bool isEnabled = false;
bool isOut;
bool isStartMarkDetected = false;
bool isOffEnabled = false;
bool isOnCross = false;
bool crossWarning = false;
bool isImpOn = false;

int speedDecrement = 0;
bool isSpeedBase = false;

float filteredError = 0;
float previousFilteredError = 0;
int CX;

int error;
int valPWMA;
int valPWMB;

String header;
String message;

int _speed_ = SPEED;
int _speedImp_ = SPEED_IMP;
int _markTimer_ = MARK_TIMER_MS;
int _crossWarningTime_ = CROSS_WARNING_TIME_MS;

bool _sensorMask_ = SENSOR_MASK;
bool _crossWarningMethod_ = CROSS_WARNING_METHOD;
bool _fixedMaxTimeValues_ = FIXED_MAX_TIME_VALUES;
bool _fixedMinTimeValues_ = FIXED_MIN_TIME_VALUES;
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

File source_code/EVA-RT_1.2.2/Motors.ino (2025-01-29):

/*
  Motors - auxilliary code for robotracer EVA-RT series

    Created on: Jan, 2025
    Edited by Mauricio Tovar
    
  Copyright (C) 2025 EXOTIC TEAM MX

  This code is the original version used in the All Chile
  Robot Contest 2025.

  This code consist of the motor control functions for the
  line following differential drive method. It allows
  control the impeller motor. It includes a testing routine.
  
  This code is part of the EVA-RT Github repository. See more
  in the next link:
  
  https://github.com/EXOTIC-TEAM-MX/EVA-RT
*/

void setImpeller(int _pwm) {
  if (areMotorsEnabled) {
    analogWrite(PIN_PWM_C, (_pwm >= 0 && _pwm <= 255) ? _pwm : 0);
  }
}

void setMotorA(int _pwm) {
  if (areMotorsEnabled) {
    analogWrite(PIN_PWM_A, abs(_pwm));

    PORTD = (_pwm > 0)   ? (PORTD & ~(1 << PORTD3))  //  forward
            : (_pwm < 0) ? (PORTD | (1 << PORTD3))   //  reverse
                         : PORTD;                    //  no change
  }
}

void setMotorB(int _pwm) {
  if (areMotorsEnabled) {
    analogWrite(PIN_PWM_B, abs(_pwm));

    PORTD = (_pwm > 0)   ? (PORTD & ~(1 << PORTD4))  //  forward
            : (_pwm < 0) ? (PORTD | (1 << PORTD4))   //  reverse
                         : PORTD;                    //  no change
  }
}

void testMotors(int _pwm, int _time) {
  delay(500);

  consoleLine("*MOTOR A+*");
  setMotorA(_pwm);
  setLED_A(DISPLAY_MODE, HIGH);
  delay(_time);
  setMotorA(0);
  setLED_A(DISPLAY_MODE, LOW);
  delay(_time + 1500);
  consoleLine("*MOTOR A-*");
  setMotorA(-_pwm);
  setLED_A(DISPLAY_MODE, HIGH);
  delay(_time);
  setMotorA(0);
  setLED_A(DISPLAY_MODE, LOW);
  delay(_time + 1500);

  consoleLine("*MOTOR B+*");
  setMotorB(_pwm);
  setLED_B(DISPLAY_MODE, HIGH);
  delay(_time);
  setMotorB(0);
  setLED_B(DISPLAY_MODE, LOW);
  delay(_time + 1500);
  consoleLine("*MOTOR B-*");
  setMotorB(-_pwm);
  setLED_B(DISPLAY_MODE, HIGH);
  delay(_time);
  setMotorB(0);
  setLED_B(DISPLAY_MODE, LOW);
  delay(_time + 1500);

  consoleLine("SELECT OPERATION> TEST WHEEL MOTORS[1] / TEST IMPELLER[2]");
}

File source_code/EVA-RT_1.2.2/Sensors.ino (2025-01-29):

/*
  Sensors - auxilliary code for robotracer EVA-RT series

    Created on: Jan, 2025
    Edited by Mauricio Tovar
    
  Copyright (C) 2025 EXOTIC TEAM MX

  This code is the original version used in the All Chile
  Robot Contest 2025.

  This code consist of reading and processing sensor data.
  It includes functions for calibrating, reading, and
  interpreting sensor values to determine the line's position.
  
  This code is part of the EVA-RT Github repository. See more
  in the next link:
  
  https://github.com/EXOTIC-TEAM-MX/EVA-RT
*/

void resetCalibrationValues() {
  for (byte i = 0; i < TOTAL_SENSORS; i++) {
    maxSensorValues[i] = 0;
    minSensorValues[i] = 255;
  }
}

void resetLinePrint() {
  for (byte i = 0; i < NUM_SENSORS; i++) {
    previousLinePrint[i] = true;
  }
}

void getSensorThreshold() {
  for (byte i = 0; i < TOTAL_SENSORS; i++) {
    sensorThreshold[i] = (maxSensorValues[i] - minSensorValues[i]) * ((float)(SENSOR_THRESHOLD_PERCENT) / 100) + minSensorValues[i];
  }
}

uint16_t readLine() {
  uint32_t avg = 0;
  uint32_t sum = 0;

  readCalibratedSensors();

  for (byte i = 0; i < NUM_SENSORS; i++) {
    if (sensorValues[i]) {
      avg += (uint32_t)sensorValues[i] * i * 1000;
      sum += sensorValues[i];
    }
  }

  return sum ? avg / sum : 0;
}


void calibrateSensors() {
  int highestSample[TOTAL_SENSORS];
  int lowestSample[TOTAL_SENSORS];

  //  samples recollector
  for (byte j = 0; j < CALIBRATION_COLLECTOR_SAMPLES; j++) {

    readSampledSensors();

    for (byte i = 0; i < TOTAL_SENSORS; i++) {
      if ((j == 0) || (sensorValues[i] > highestSample[i])) {
        highestSample[i] = sensorValues[i];
      }

      if ((j == 0) || (sensorValues[i] < lowestSample[i])) {
        lowestSample[i] = sensorValues[i];
      }
    }
  }

  for (byte i = 0; i < TOTAL_SENSORS; i++) {
    if (lowestSample[i] > maxSensorValues[i]) {
      maxSensorValues[i] = lowestSample[i];
    }
    if (highestSample[i] < minSensorValues[i]) {
      minSensorValues[i] = highestSample[i];
    }
  }
}

void readCalibratedSensors() {
  isOnLine = false;
  readRawSensors();

  for (byte i = 0; i < NUM_SENSORS; i++) {
    unsigned int range = maxSensorValues[i] - sensorThreshold[i];

    if (sensorValues[i] > sensorThreshold[i]) {
      isOnLine = true;
      if (sensorValues[i] < maxSensorValues[i]) {
        sensorValues[i] = ((sensorValues[i] - sensorThreshold[i]) * 255) / range;
      } else {
        sensorValues[i] = 255;
      }
    } else {
      sensorValues[i] = 0;
    }
  }

  sensorValues[INDEX_MS0] = sensorValues[INDEX_MS0] > sensorThreshold[INDEX_MS0] ? 1 : 0;
  sensorValues[INDEX_MS1] = sensorValues[INDEX_MS1] > sensorThreshold[INDEX_MS1] ? 1 : 0;

  if (isOnLine) {
    //  set last detected side
    lastDetectedSide = (sensorValues[0] || sensorValues[1])                               ? 0
                       : (sensorValues[NUM_SENSORS - 1] || sensorValues[NUM_SENSORS - 2]) ? 1
                                                                                          : lastDetectedSide;
  }

  if (_sensorMask_) {
    //  clear previous sensor print
    for (byte i = 0; i < NUM_SENSORS; i++) {
      previousLinePrint[i] = 0;
    }

    // update previous sensor print
    for (byte i = 0; i < NUM_SENSORS; i++) {
      if (sensorValues[i]) {
        previousLinePrint[i] = true;

        //  one sensor adyacent
        //if (i) previousLinePrint[i - 1] = true;
        //if (i < NUM_SENSORS - 1) previousLinePrint[i + 1] = true;

        //  two sensor adyacent
        if (i > 1) {
          previousLinePrint[i - 1] = true;
          previousLinePrint[i - 2] = true;
        }
        if (i < NUM_SENSORS - 2) {
          previousLinePrint[i + 1] = true;
          previousLinePrint[i + 2] = true;
        }
      }
    }

    if (!isOnLine) {
      previousLinePrint[lastDetectedSide ? (NUM_SENSORS - 1) : 0] = true;
      previousLinePrint[lastDetectedSide ? (NUM_SENSORS - 2) : 1] = true;
    }
  }

  //  cross methods
  if (sensorValues[(NUM_SENSORS / 2) - CROSS_SENSOR_OFSET - 1] && sensorValues[(NUM_SENSORS / 2) + CROSS_SENSOR_OFSET]) {
    isOnCross = true;
    crossStartTime = currentTime;
    crossWarning = true;
    isOffEnabled = _crossWarningMethod_ ? false : isEnabled;
    setLED_B(DM_CROSS_METHODS, HIGH);
  } else {
    isOnCross = false;
  }

  //  reset cross warning timer
  if (crossWarning && currentTime - crossStartTime >= _crossWarningTime_) {
    crossWarning = false;
    setLED_B(DM_CROSS_METHODS, LOW);
  }

  setLED_A(DM_CROSS_METHODS, isOnCross);
}

void readSampledSensors() {
  int sumSensorValues[NUM_SENSORS + 2];

  for (byte i = 0; i < NUM_SENSORS + 2; i++) {
    sumSensorValues[i] = 0;
  }

  for (byte j = 0; j < CALIBRATION_AVG_SAMPLES; j++) {
    readRawSensors();

    for (byte i = 0; i < NUM_SENSORS; i++) {
      sumSensorValues[i] += sensorValues[i];
    }

    sumSensorValues[INDEX_MS0] += sensorValues[INDEX_MS0];
    sumSensorValues[INDEX_MS1] += sensorValues[INDEX_MS1];
  }

  for (byte i = 0; i < NUM_SENSORS; i++) {
    sensorValues[i] = (sumSensorValues[i] + (CALIBRATION_AVG_SAMPLES >> 1)) / CALIBRATION_AVG_SAMPLES;
  }

  sensorValues[INDEX_MS0] = (sumSensorValues[INDEX_MS0] + (CALIBRATION_AVG_SAMPLES >> 1)) / CALIBRATION_AVG_SAMPLES;
  sensorValues[INDEX_MS1] = (sumSensorValues[INDEX_MS1] + (CALIBRATION_AVG_SAMPLES >> 1)) / CALIBRATION_AVG_SAMPLES;
}

void readRawSensors() {
  //  read GND
  selectADCChannel(ADC_GND_CHANNEL);
  startADCConversion();
  waitForADC();
  disableADC();

  selectADCChannel(ADC_MUX_CHANNEL);

  for (byte i = FIRST_SENSOR_SWITCH_CONFIG; i <= LAST_SENSOR_SWITCH_CONFIG; i++) {
    if (!_sensorMask_ || previousLinePrint[i - FIRST_SENSOR_SWITCH_CONFIG]) {
      PORTC = (PORTC & ~0b1111) | i;  //  set switch address

      //  read MUX
      startADCConversion();
      waitForADC();
      sensorValues[i - FIRST_SENSOR_SWITCH_CONFIG] = ADCH;
      disableADC();
    } else {
      sensorValues[i - FIRST_SENSOR_SWITCH_CONFIG] = INVERT_SENSOR_READS ? 255 : 0;
    }
    sensorValues[i - FIRST_SENSOR_SWITCH_CONFIG] = INVERT_SENSOR_READS ? 255 - sensorValues[i - FIRST_SENSOR_SWITCH_CONFIG] : sensorValues[i - FIRST_SENSOR_SWITCH_CONFIG];
  }

  //  read MS0
  selectADCChannel(ADC_MARK_SENSOR_0);
  startADCConversion();
  waitForADC();
  sensorValues[INDEX_MS0] = INVERT_SENSOR_READS ? 255 - ADCH : ADCH;
  disableADC();

  //  read MS1
  selectADCChannel(ADC_MARK_SENSOR_1);
  startADCConversion();
  waitForADC();
  sensorValues[INDEX_MS1] = INVERT_SENSOR_READS ? 255 - ADCH : ADCH;
  disableADC();
}

void printSensorValues() {
  for (byte i = 0; i < NUM_SENSORS; i++) {
    Serial.print(String(sensorValues[i]) + "\t");
  }
  Serial.println("\t" + String(sensorValues[INDEX_MS0]) + "\t" + String(sensorValues[INDEX_MS1]));
}

void printPreviousSensorPrint() {
  for (byte i = 0; i < NUM_SENSORS; i++) {
    Serial.print(previousLinePrint[i]);
    Serial.print("\t");
  }
  Serial.println();
}
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

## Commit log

2025-02-03 Files updated and gerbers added
2025-03-11 Las side detected correction.ino
    [EVA-RT_LITE_1.0.ino]
2025-05-28 Comments and naming correction
    "dx" variable name was out of context
    [EVA-RT_LITE_1.0.ino]

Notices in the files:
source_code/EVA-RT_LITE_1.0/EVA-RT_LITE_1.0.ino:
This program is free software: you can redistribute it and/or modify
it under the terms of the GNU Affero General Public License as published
